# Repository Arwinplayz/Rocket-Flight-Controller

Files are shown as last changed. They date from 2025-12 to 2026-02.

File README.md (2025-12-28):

# Custom Flight Controller
A custom Flight Controller maded within kicad, specificaly for rockets.
---

## Project Overview
The goal was to create a custom Flight Controller which was capable of utilising TVC to guide a rocket.

---

## Screenshots

### 1. Overall
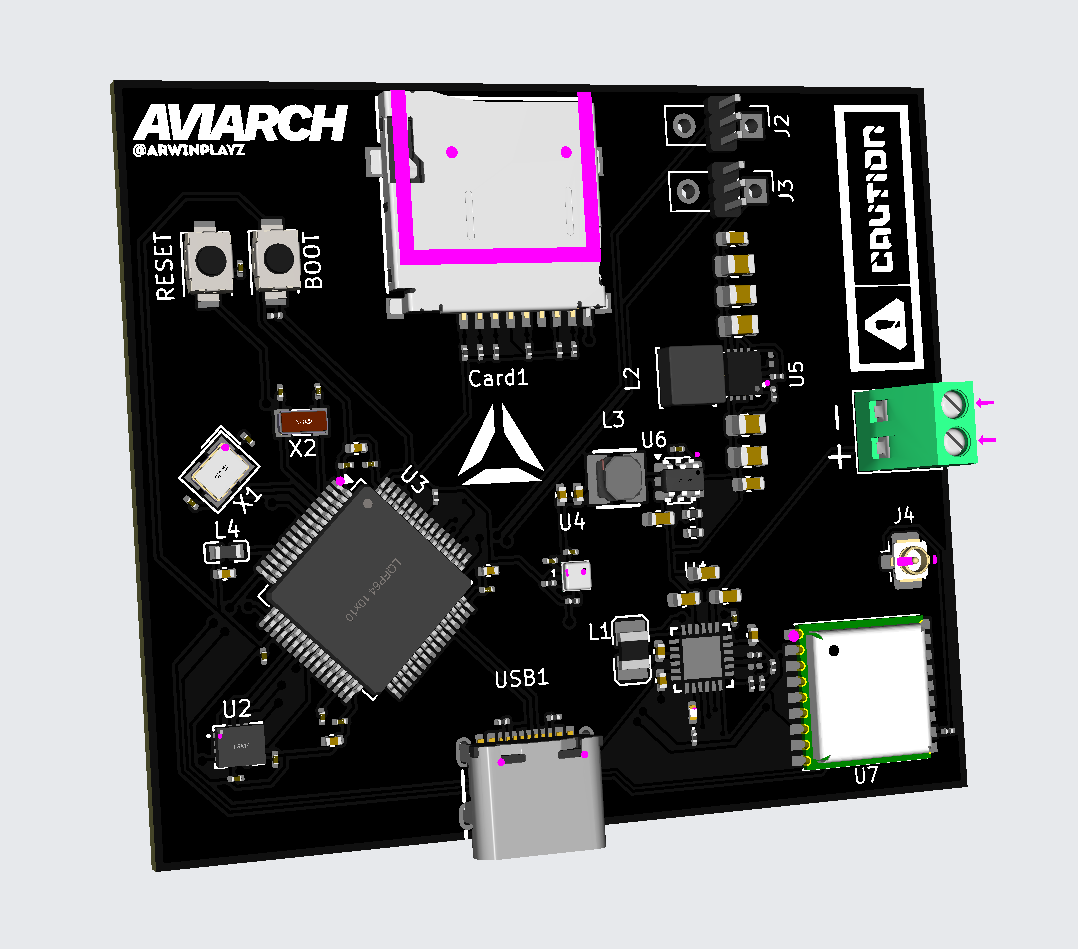
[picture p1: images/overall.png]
Flight Controller Screenshot
  

### 2. Schematic
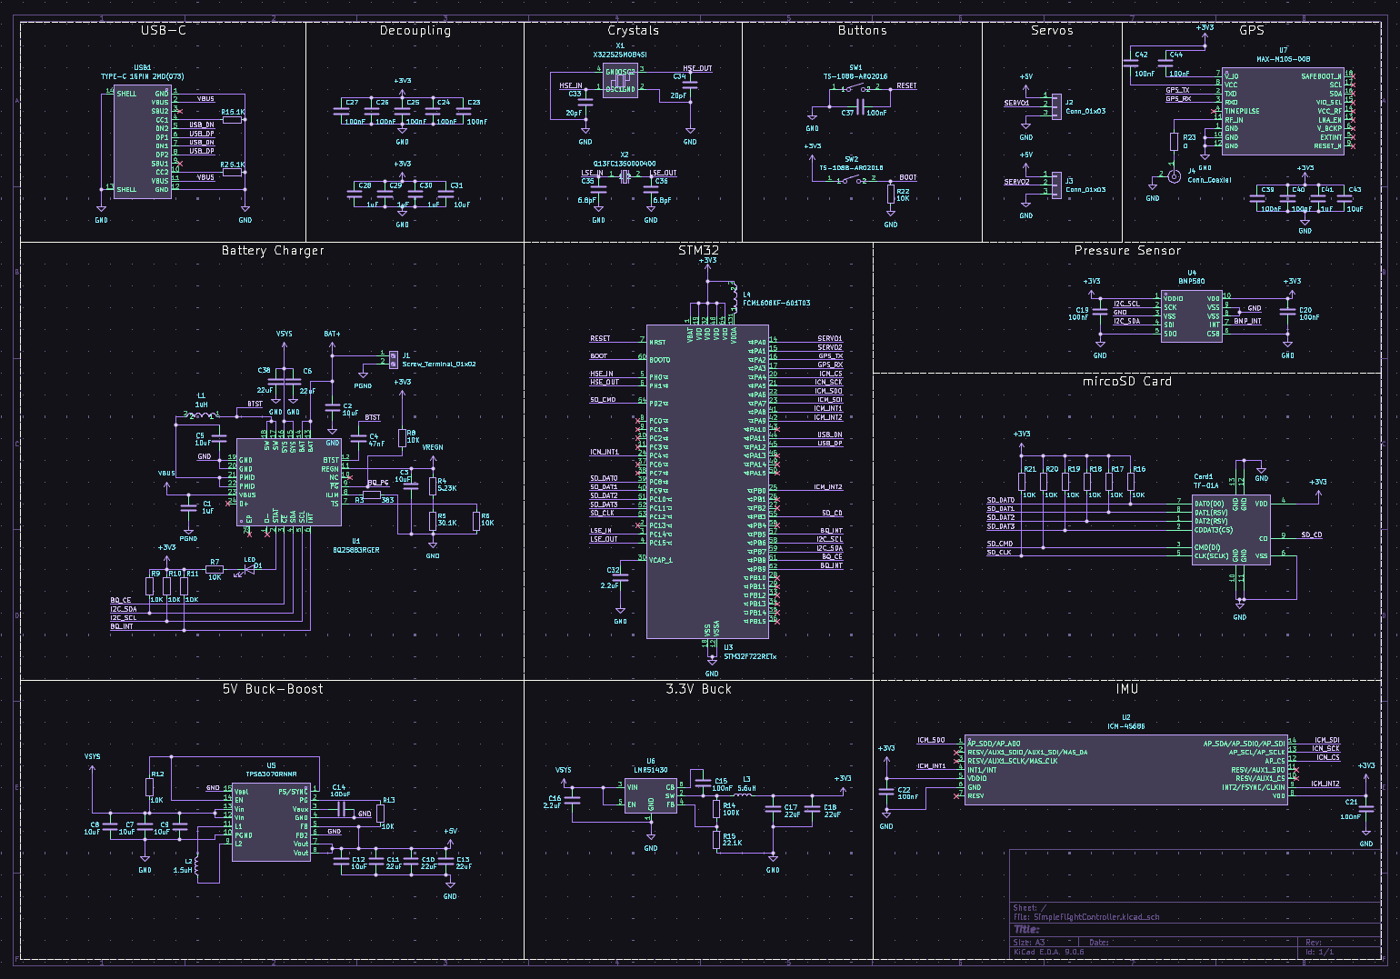
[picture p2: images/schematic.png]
Schematic Screenshot
  

### 3. PCB layout
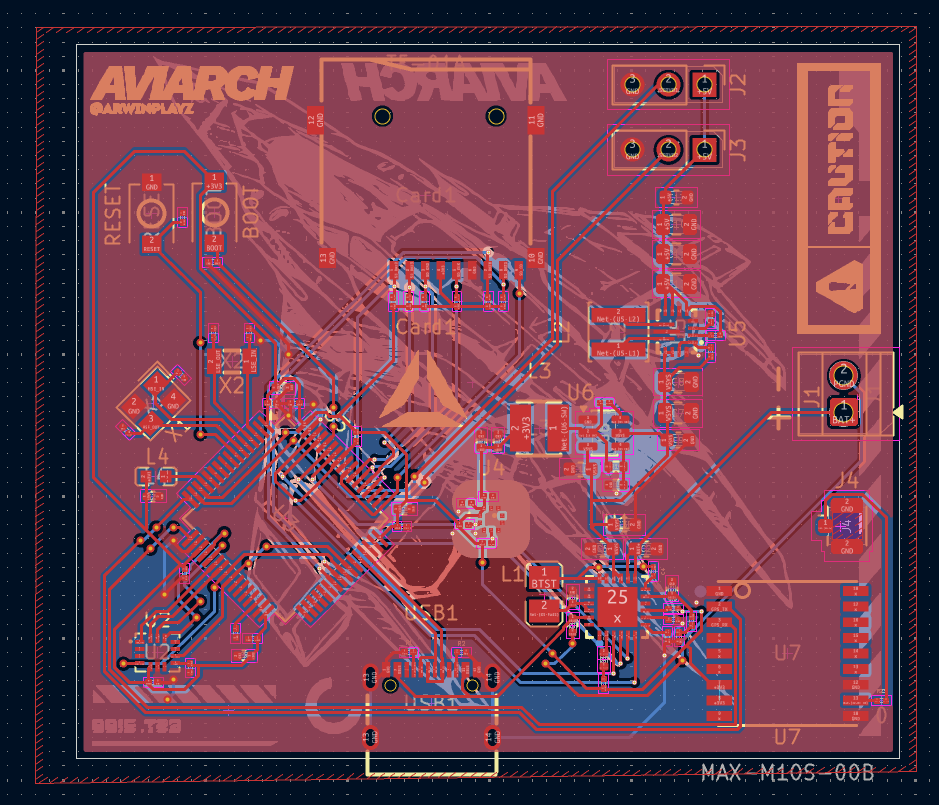
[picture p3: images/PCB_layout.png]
PCB Screenshot
  

### 4. Design
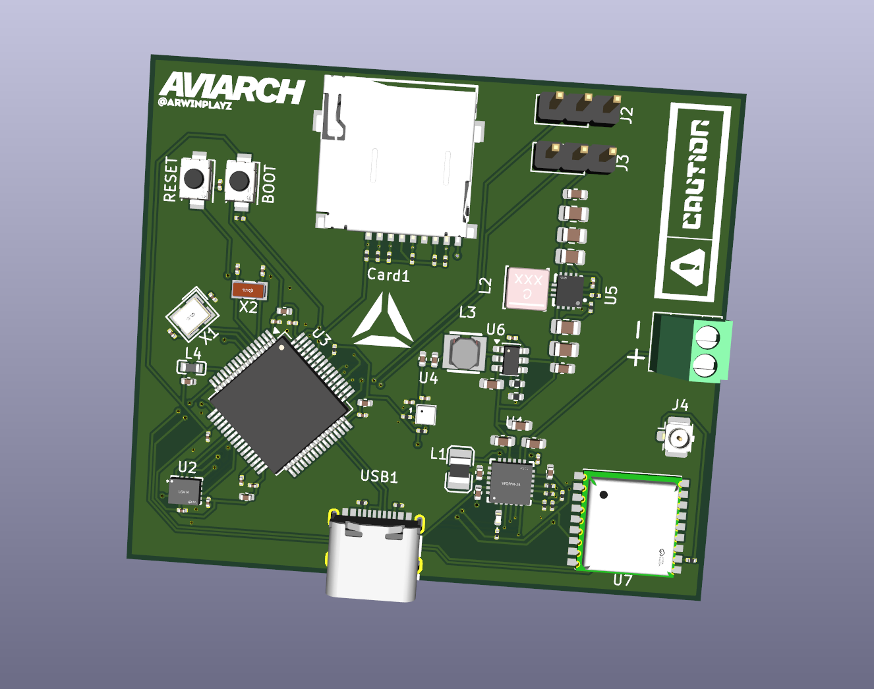
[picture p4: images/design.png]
Design Screenshot


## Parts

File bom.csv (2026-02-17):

Designator | Footprint | Quantity | Value | LCSC Part #
BOOT, RESET | SW-SMD_L3.9-W3.0-P4.45 | 2 | TS-1088-AR02016 | C720477
C1, C28, C29, C30 | 0402 | 4 | 1uF
C10, C11, C13 | 0805 | 3 | 22uF
C12, C2, C9 | 0603 | 3 | 10uF
C14 | 0201 | 1 | 100uF
C15, C19, C20, C21, C22, C23, C24, C25, C26, C27, C37 | 0201 | 11 | 100nF
C16 | 0603 | 1 | 2.2uF
C17, C18 | 0402 | 2 | 22uF
C3, C31, C5 | 0402 | 3 | 10uF
C32 | 0201 | 1 | 2.2uF
C33, C34 | 0201 | 2 | 20pF
C35, C36 | 0201 | 2 | 6.8pF
C38, C6 | 0603 | 2 | 22uF
C4 | 0201 | 1 | 47nF
C7, C8 | 0805 | 2 | 10uF
CARD1 | TF-SMD_TF-01A | 1 | TF-01A | C91145
D1 | 0402 | 1 | LED
J1 | TerminalBlock_Xinya_XY308-2.54-2P_1x02_P2.54mm_Horizontal | 1 | Screw_Terminal_01x02
J2, J3 | PinHeader_1x03_P2.54mm_Vertical | 2 | Conn_01x03
J4 | U.FL_Hirose_U.FL-R-SMT-1_Vertical | 1 | Conn_Coaxial
L1 | L2520 | 1 | 1uH | C435392
L2 | IND-SMD_L4.0-W4.0-A | 1 | 1.5uH
L3 | IND-SMD_L3.0-W3.0 | 1 | 5.6uH
L4 | L0603 | 1 | FCM1608KF-601T03 | C141723
R1, R2 | 0201 | 2 | 5.1K
R10, R11, R12, R13, R16, R17, R18, R19, R20, R21, R22, R6, R7, R8, R9 | 0201 | 15 | 10K
R14 | 0402 | 1 | 100K
R15 | 0402 | 1 | 22.1K
R23 | 0201 | 1 | 0
R3 | 0201 | 1 | 383
R4 | 0201 | 1 | 5.23K
R5 | 0201 | 1 | 30.1K
U1 | VFQFPN-24_L4.0-W4.0-P0.50-BL-EP2.8 | 1 | BQ25883RGER | C544362
U2 | LGA-14_L3.0-W2.5-P0.50-TL | 1 | ICM-45686 | C22459454
U3 | LQFP-64_10x10mm_P0.5mm | 1 | STM32F722RETx
U4 | LGA-10_L2.0-W2.0-P0.50-TL_BMP580 | 1 | BMP580 | C22391138
U5 | VQFN-HR-15_L3.0-W2.5-P0.50-BL_TPS63070RNMR | 1 | TPS63070RNMR | C109322
U6 | SOT-23-6 | 1 | LMR51430
U7 | SMD-18_L10.1-W9.7-P1.10-TL_SKG09F | 1 | MAX-M10S-00B | C4153167
USB1 | USB-C-SMD_TYPE-C-6PIN-2MD-073 | 1 | TYPE-C 16PIN 2MD(073) | C2765186
X1 | CRYSTAL-SMD_4P-L3.2-W2.5-BL | 1 | X322525MOB4SI | C9006
X2 | FC-135R_L3.2-W1.5 | 1 | Q13FC1350000400 | C32346

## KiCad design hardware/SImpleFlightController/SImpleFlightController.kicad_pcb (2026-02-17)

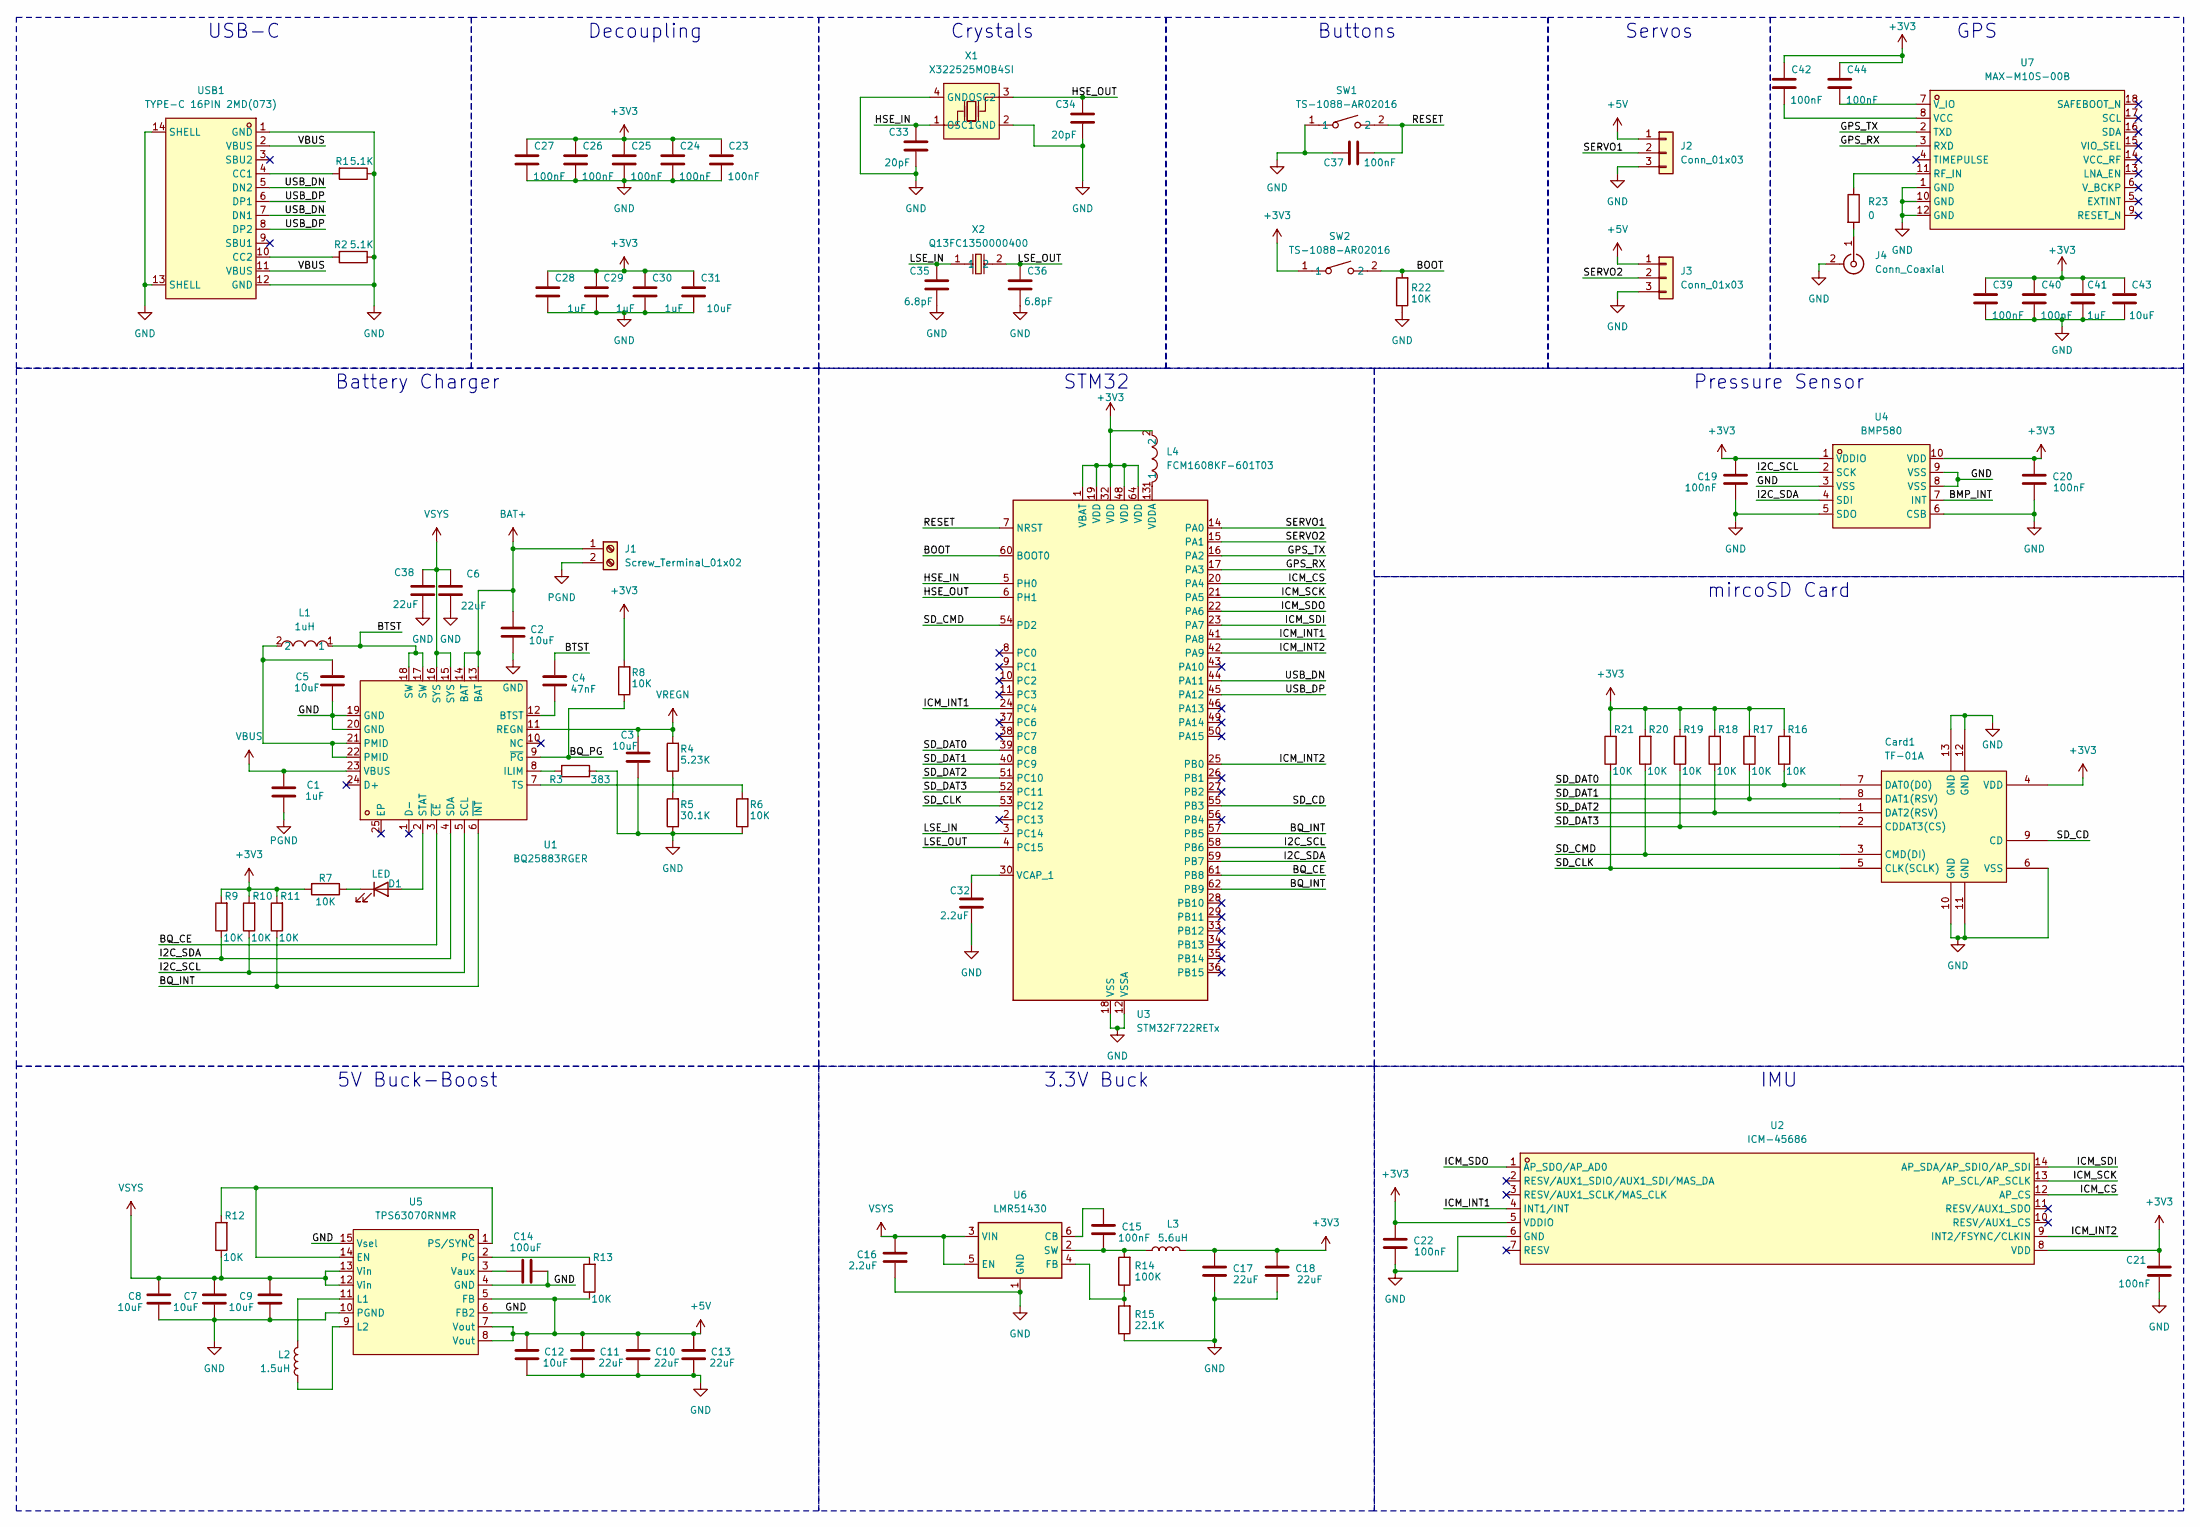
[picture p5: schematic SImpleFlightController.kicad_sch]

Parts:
C1, C28, C29, C30, C41: 1uF; C_0402_1005Metric
C2, C9, C12: 10uF; C_0603_1608Metric
C3, C5, C31, C43: 10uF; C_0402_1005Metric
C4: 47nF; C_0201_0603Metric
C6, C38: 22uF; C_0603_1608Metric
C7, C8: 10uF; C_0805_2012Metric
C10, C11, C13: 22uF; C_0805_2012Metric
C14: 100uF; C_0201_0603Metric
C15, C19, C20, C21, C22, C23, C24, C25, C26, C27, C37: 100nF; C_0201_0603Metric
C16: 2.2uF; C_0603_1608Metric
C17, C18: 22uF; C_0402_1005Metric
C32: 2.2uF; C_0201_0603Metric
C33, C34: 20pF; C_0201_0603Metric
C35, C36: 6.8pF; C_0201_0603Metric
C39, C40, C42, C44: 100nF; C_0402_1005Metric
Card1: TF-01A; TF-SMD_TF-01A; LCSC Part C91145
D1: LED; LED_0402_1005Metric
J1: Screw_Terminal_01x02; TerminalBlock_Xinya_XY308-2.54-2P_1x02_P2.54mm_Horizontal
J2, J3: Conn_01x03; PinHeader_1x03_P2.54mm_Vertical
J4: Conn_Coaxial; U.FL_Hirose_U.FL-R-SMT-1_Vertical
L1: 1uH; L2520; LCSC Part C435392
L2: 1.5uH; IND-SMD_L4.0-W4.0-A
L3: 5.6uH; IND-SMD_L3.0-W3.0
L4: FCM1608KF-601T03; L0603; LCSC Part C141723
R1, R2: 5.1K; R_0201_0603Metric
R3: 383; R_0201_0603Metric
R4: 5.23K; R_0201_0603Metric
R5: 30.1K; R_0201_0603Metric
R6, R7, R8, R9, R10, R11, R12, R13, R16, R17, R18, R19, R20, R21, R22: 10K; R_0201_0603Metric
R14: 100K; R_0402_1005Metric
R15: 22.1K; R_0402_1005Metric
R23: 0; R_0201_0603Metric
SW1, SW2: TS-1088-AR02016; SW-SMD_L3.9-W3.0-P4.45; LCSC Part C720477
U1: BQ25883RGER; VFQFPN-24_L4.0-W4.0-P0.50-BL-EP2.8; LCSC Part C544362
U2: ICM-45686; LGA-14_L3.0-W2.5-P0.50-TL; LCSC Part C22459454
U3: STM32F722RETx; LQFP-64_10x10mm_P0.5mm
U4: BMP580; LGA-10_L2.0-W2.0-P0.50-TL_BMP580; LCSC Part C22391138
U5: TPS63070RNMR; VQFN-HR-15_L3.0-W2.5-P0.50-BL_TPS63070RNMR; LCSC Part C109322
U6: LMR51430; SOT-23-6
U7: MAX-M10S-00B; SMD-18_L10.1-W9.7-P1.10-TL_SKG09F; LCSC Part C4153167
USB1: TYPE-C 16PIN 2MD(073); USB-C-SMD_TYPE-C-6PIN-2MD-073; LCSC Part C2765186
X1: X322525MOB4SI; CRYSTAL-SMD_4P-L3.2-W2.5-BL; LCSC Part C9006
X2: Q13FC1350000400; FC-135R_L3.2-W1.5; LCSC Part C32346

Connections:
+3V3: C17.1, C18.1, C19.1, C20.1, C21.1, C22.1, C23.1, C24.1, C25.1, C26.1, C27.1, C28.1, C29.1, C30.1, C31.1, C39.1, C40.1, C41.1, C42.1, C42.2, C43.1, C44.1, C44.2, Card1.4 (VDD), L3.2, L4.2, R7.2, R8.2, R9.2, R10.2, R11.2, R16.2, R17.2, R18.2, R19.2, R20.2, R21.2, SW2.1, U2.5 (VDDIO), U2.8 (VDD), U3.1 (VBAT), U3.19 (VDD), U3.32 (VDD), U3.48 (VDD), U3.64 (VDD), U4.1 (VDDIO), U4.10 (VDD), U7.7 (V_IO), U7.8 (VCC); also elsewhere on the board
+5V: C10.1, C11.1, C12.1, C13.1, J2.1, J3.1, R13.1, U5.5 (FB), U5.7 (Vout), U5.8 (Vout)
/BMP_INT: U4.7 (INT)
/BOOT: R22.2, SW2.2, U3.60 (BOOT0); also elsewhere on the board
/BQ_CE: U1.3 (~CE), U3.61 (PB8)
/BQ_INT: R11.1, U1.6 (~INT), U3.57 (PB5), U3.62 (PB9)
/BQ_PG: R8.1, U1.9 (~PG)
/BTST: C4.1, L1.1, U1.17 (SW), U1.18 (SW)
/GPS_RX: U3.17 (PA3), U7.3 (RXD)
/GPS_TX: U3.16 (PA2), U7.2 (TXD)
/HSE_IN: C33.1, U3.5 (PH0), X1.1 (OSC1)
/HSE_OUT: C34.1, U3.6 (PH1), X1.3 (OSC2)
/I2C_SCL: R10.1, U1.5 (SCL), U3.58 (PB6), U4.2 (SCK)
/I2C_SDA: R9.1, U1.4 (SDA), U3.59 (PB7), U4.4 (SDI)
/ICM_CS: U2.12 (AP_CS), U3.20 (PA4)
/ICM_INT1: U2.4 (INT1/INT), U3.24 (PC4), U3.41 (PA8)
/ICM_INT2: U2.9 (INT2/FSYNC/CLKIN), U3.25 (PB0), U3.42 (PA9)
/ICM_SCK: U2.13 (AP_SCL/AP_SCLK), U3.21 (PA5)
/ICM_SDI: U2.14 (AP_SDA/AP_SDIO/AP_SDI), U3.23 (PA7)
/ICM_SDO: U2.1 (AP_SDO/AP_AD0), U3.22 (PA6)
/LSE_IN: C35.1, U3.3 (PC14), X2.1
/LSE_OUT: C36.1, U3.4 (PC15), X2.2
/RESET: C37.2, SW1.2, U3.7 (NRST); also elsewhere on the board
/SD_CD: Card1.9 (CD), U3.55 (PB3)
/SD_CLK: Card1.5 (CLK(SCLK)), R21.1, U3.53 (PC12)
/SD_CMD: Card1.3 (CMD(DI)), R20.1, U3.54 (PD2)
/SD_DAT0: Card1.7 (DAT0(D0)), R16.1, U3.39 (PC8)
/SD_DAT1: Card1.8 (DAT1(RSV)), R17.1, U3.40 (PC9)
/SD_DAT2: Card1.1 (DAT2(RSV)), R18.1, U3.51 (PC10)
/SD_DAT3: Card1.2 (CDDAT3(CS)), R19.1, U3.52 (PC11)
/SERVO1: J2.2, U3.14 (PA0)
/SERVO2: J3.2, U3.15 (PA1)
/USB_DN: U3.44 (PA11), USB1.5 (DN2), USB1.7 (DN1)
/USB_DP: U3.45 (PA12), USB1.6 (DP1), USB1.8 (DP2)
BAT+: C2.1, J1.1, U1.13 (BAT), U1.14 (BAT)
GND: C2.2, C3.2, C5.2, C6.2, C7.2, C8.2, C9.2, C10.2, C11.2, C12.2, C13.2, C14.1, C16.2, C17.2, C18.2, C19.2, C20.2, C21.2, C22.2, C23.2, C24.2, C25.2, C26.2, C27.2, C28.2, C29.2, C30.2, C31.2, C32.2, C33.2, C34.2, C35.2, C36.2, C37.1, C38.2, C39.2, C40.2, C41.2, C43.2, Card1.6 (VSS), Card1.10 (GND), Card1.11 (GND), Card1.12 (GND), Card1.13 (GND), J2.3, J3.3, J4.2 (Ext), R1.1, R2.1, R3.1, R5.1, R6.1, R15.1, R22.1, SW1.1, U1.19 (GND), U1.20 (GND), U2.6 (GND), U3.12 (VSSA), U3.18 (VSS), U3.31 (VSS), U3.47 (VSS), U3.63 (VSS), U4.3 (VSS), U4.5 (SDO), U4.6 (CSB), U4.8 (VSS), U4.9 (VSS), U5.4 (GND), U5.6 (FB2), U5.10 (PGND), U5.15 (Vsel), U6.1 (GND), U7.1 (GND), U7.10 (GND), U7.12 (GND), USB1.1 (GND), USB1.12 (GND), USB1.13 (SHELL), USB1.14 (SHELL), X1.2 (GND), X1.4 (GND); also elsewhere on the board
unnamed: C5.1, L1.2, U1.21 (PMID), U1.22 (PMID)
unnamed: D1.2 (A), U1.2 (STAT)
unnamed: D1.1 (K), R7.1
unnamed: J4.1 (In), R23.2
unnamed: R4.1, R5.2
unnamed: C4.2, U1.12 (BTST)
unnamed: R3.2, U1.8 (ILIM)
unnamed: R6.2, U1.7 (TS)
unnamed: C32.1, U3.30 (VCAP_1)
unnamed: L4.1, U3.13 (VDDA)
unnamed: R12.2, U5.1 (PS/SYNC), U5.14 (EN)
unnamed: L2.1, U5.11 (L1)
unnamed: L2.2, U5.9 (L2)
unnamed: R13.2, U5.2 (PG)
unnamed: C14.2, U5.3 (Vaux)
unnamed: C15.1, U6.6 (CB)
unnamed: R14.1, R15.2, U6.4 (FB)
unnamed: C15.2, L3.1, R14.2, U6.2 (SW)
unnamed: R23.1, U7.11 (RF_IN)
unnamed: R1.2, USB1.4 (CC1)
unnamed: R2.2, USB1.10 (CC2)
PGND: C1.2, J1.2
VBUS: C1.1, U1.23 (VBUS), USB1.2 (VBUS), USB1.11 (VBUS)
VREGN: C3.1, R4.2, U1.11 (REGN)
VSYS: C6.1, C7.1, C8.1, C9.1, C16.1, C38.1, R12.1, U1.15 (SYS), U1.16 (SYS), U5.12 (Vin), U5.13 (Vin), U6.3 (VIN), U6.5 (EN)

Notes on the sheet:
Buttons
mircoSD Card
USB-C
Crystals
GPS
Servos
Battery Charger
STM32
IMU
5V Buck-Boost
Pressure Sensor
Decoupling
3.3V Buck

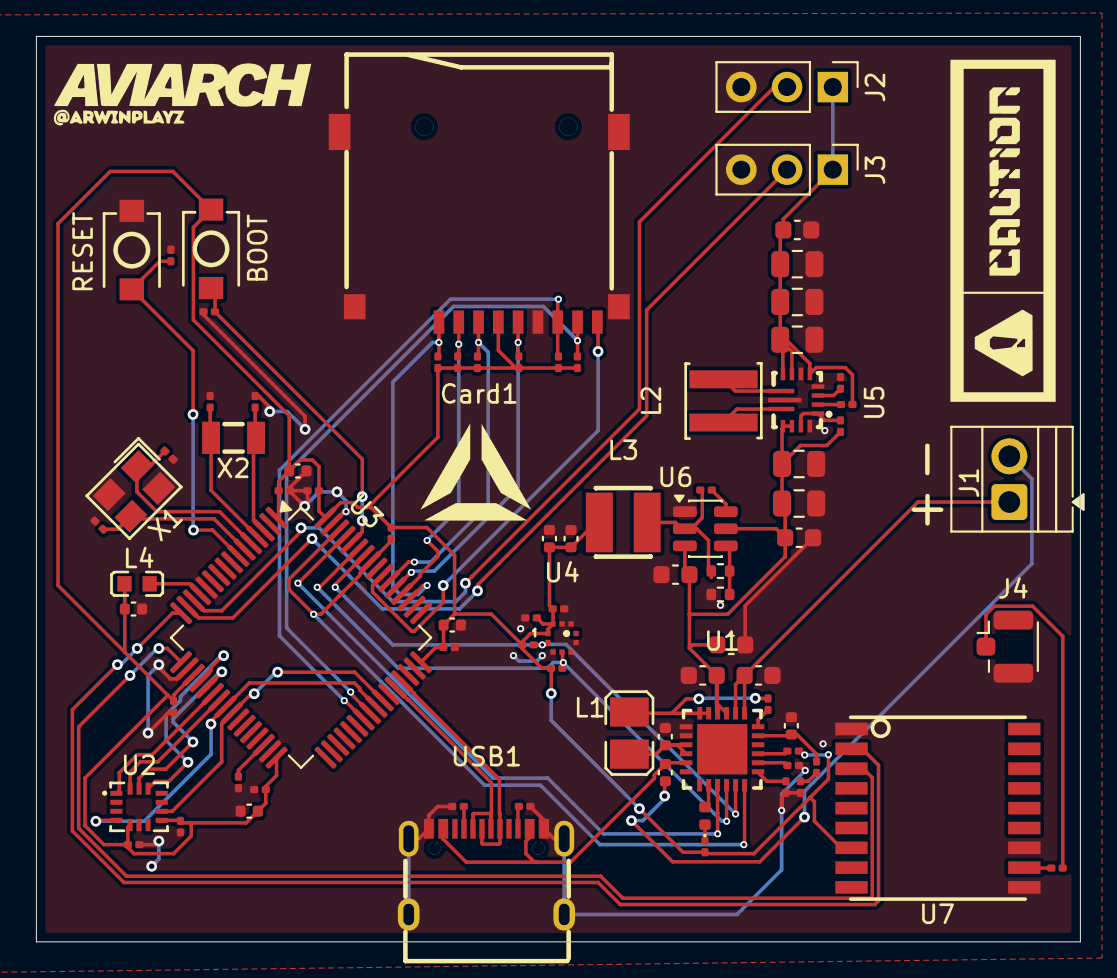
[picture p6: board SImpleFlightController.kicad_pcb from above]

Board: 2 copper layers, 58.0 x 50.3 mm, 83 parts (0 on the bottom side), 60 nets.

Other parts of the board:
BOOT: TS-1088-AR02016; SW-SMD_L3.9-W3.0-P4.45
RESET: TS-1088-AR02016; SW-SMD_L3.9-W3.0-P4.45

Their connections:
+3V3: BOOT.1; also elsewhere on the board
/BOOT: BOOT.2; also elsewhere on the board
/RESET: RESET.2; also elsewhere on the board
GND: RESET.1; also elsewhere on the board

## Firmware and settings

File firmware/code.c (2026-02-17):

#include "stm32f7xx_hal.h"
#include <math.h>

I2C_HandleTypeDef hi2c1;
TIM_HandleTypeDef htim3;

#define IMU_I2C_ADDR (0x68 << 1)
#define IMU_REG_WHO_AM_I 0x75
#define IMU_REG_PWR_MGMT 0x06
#define IMU_REG_ACCEL_XOUT_H 0x2D
#define IMU_REG_GYRO_XOUT_H 0x33

#define SERVO_TIMER htim3
#define SERVO_CHANNEL TIM_CHANNEL_1
#define SERVO_PWM_FREQ_HZ 50.0f
#define SERVO_MIN_PULSE_US 1000.0f
#define SERVO_MAX_PULSE_US 2000.0f

#define LOOP_DT_S 0.002f
#define COMPLEMENTARY_ALPHA 0.98f

void SystemClock_Config(void);
static void MX_GPIO_Init(void);
static void MX_I2C1_Init(void);
static void MX_TIM3_Init(void);

static void IMU_Init(void);
static void IMU_ReadRaw(int16_t *ax, int16_t *az, int16_t *gx);
static float map_pitch_to_pulse(float pitch_deg);

int main(void)
{
    HAL_Init();
    SystemClock_Config();
    MX_GPIO_Init();
    MX_I2C1_Init();
    MX_TIM3_Init();
    IMU_Init();
    HAL_TIM_PWM_Start(&SERVO_TIMER, SERVO_CHANNEL);

    float pitch_deg = 0.0f;

    while (1)
    {
        static uint32_t last_tick = 0;
        uint32_t now = HAL_GetTick();
        if (now - last_tick < (uint32_t)(LOOP_DT_S * 1000.0f)) continue;
        last_tick = now;

        int16_t ax_raw, az_raw, gx_raw;
        IMU_ReadRaw(&ax_raw, &az_raw, &gx_raw);

        float ax = (float)ax_raw / 16384.0f;
        float az = (float)az_raw / 16384.0f;
        float gx = (float)gx_raw / 131.0f;

        float pitch_acc = atan2f(-ax, az) * 180.0f / (float)M_PI;
        float pitch_gyro = pitch_deg + gx * LOOP_DT_S;
        pitch_deg = COMPLEMENTARY_ALPHA * pitch_gyro + (1.0f - COMPLEMENTARY_ALPHA) * pitch_acc;

        float pulse_us = map_pitch_to_pulse(pitch_deg);

        uint32_t timer_clk = HAL_RCC_GetPCLK1Freq() * 2;
        float timer_freq = 1000000.0f;
        uint32_t period = (uint32_t)(timer_freq / SERVO_PWM_FREQ_HZ) - 1;
        uint32_t compare = (uint32_t)((pulse_us / 1000000.0f) * timer_freq);

        __HAL_TIM_SET_AUTORELOAD(&SERVO_TIMER, period);
        __HAL_TIM_SET_COMPARE(&SERVO_TIMER, SERVO_CHANNEL, compare);
    }
}

static void IMU_WriteReg(uint8_t reg, uint8_t val)
{
    HAL_I2C_Mem_Write(&hi2c1, IMU_I2C_ADDR, reg, I2C_MEMADD_SIZE_8BIT, &val, 1, 100);
}

static void IMU_ReadRegs(uint8_t reg, uint8_t *buf, uint16_t len)
{
    HAL_I2C_Mem_Read(&hi2c1, IMU_I2C_ADDR, reg, I2C_MEMADD_SIZE_8BIT, buf, len, 100);
}

static void IMU_Init(void)
{
    HAL_Delay(100);
    IMU_WriteReg(IMU_REG_PWR_MGMT, 0x00);
    HAL_Delay(10);
}

static void IMU_ReadRaw(int16_t *ax, int16_t *az, int16_t *gx)
{
    uint8_t buf[12];
    IMU_ReadRegs(IMU_REG_ACCEL_XOUT_H, buf, 12);

    *ax = (int16_t)((buf[0] << 8) | buf[1]);
    *az = (int16_t)((buf[4] << 8) | buf[5]);
    *gx = (int16_t)((buf[8] << 8) | buf[9]);
}

static float map_pitch_to_pulse(float pitch_deg)
{
    if (pitch_deg < -45.0f) pitch_deg = -45.0f;
    if (pitch_deg > 45.0f) pitch_deg = 45.0f;
    float t = (pitch_deg + 45.0f) / 90.0f;
    return SERVO_MIN_PULSE_US + t * (SERVO_MAX_PULSE_US - SERVO_MIN_PULSE_US);
}

void SystemClock_Config(void)
{
    RCC_OscInitTypeDef RCC_OscInitStruct = {0};
    RCC_ClkInitTypeDef RCC_ClkInitStruct = {0};

    __HAL_RCC_PWR_CLK_ENABLE();
    __HAL_PWR_VOLTAGESCALING_CONFIG(PWR_REGULATOR_VOLTAGE_SCALE1);

    RCC_OscInitStruct.OscillatorType = RCC_OSCILLATORTYPE_HSE;
    RCC_OscInitStruct.HSEState = RCC_HSE_ON;
    RCC_OscInitStruct.PLL.PLLState = RCC_PLL_ON;
    RCC_OscInitStruct.PLL.PLLSource = RCC_PLLSOURCE_HSE;
    RCC_OscInitStruct.PLL.PLLM = 8;
    RCC_OscInitStruct.PLL.PLLN = 216;
    RCC_OscInitStruct.PLL.PLLP = RCC_PLLP_DIV2;
    RCC_OscInitStruct.PLL.PLLQ = 9;
    HAL_RCC_OscConfig(&RCC_OscInitStruct);

    HAL_PWREx_EnableOverDrive();

    RCC_ClkInitStruct.ClockType = RCC_CLOCKTYPE_HCLK | RCC_CLOCKTYPE_SYSCLK |
                                  RCC_CLOCKTYPE_PCLK1 | RCC_CLOCKTYPE_PCLK2;
    RCC_ClkInitStruct.SYSCLKSource = RCC_SYSCLKSOURCE_PLLCLK;
    RCC_ClkInitStruct.AHBCLKDivider = RCC_SYSCLK_DIV1;
    RCC_ClkInitStruct.APB1CLKDivider = RCC_HCLK_DIV4;
    RCC_ClkInitStruct.APB2CLKDivider = RCC_HCLK_DIV2;
    HAL_RCC_ClockConfig(&RCC_ClkInitStruct, FLASH_LATENCY_7);
}

static void MX_I2C1_Init(void)
{
    __HAL_RCC_I2C1_CLK_ENABLE();

    hi2c1.Instance = I2C1;
    hi2c1.Init.Timing = 0x20404768;
    hi2c1.Init.OwnAddress1 = 0;
    hi2c1.Init.AddressingMode = I2C_ADDRESSINGMODE_7BIT;
    hi2c1.Init.DualAddressMode = I2C_DUALADDRESS_DISABLE;
    hi2c1.Init.OwnAddress2 = 0;
    hi2c1.Init.OwnAddress2Masks = I2C_OA2_NOMASK;
    hi2c1.Init.GeneralCallMode = I2C_GENERALCALL_DISABLE;
    hi2c1.Init.NoStretchMode = I2C_NOSTRETCH_DISABLE;
    HAL_I2C_Init(&hi2c1);
    HAL_I2CEx_ConfigAnalogFilter(&hi2c1, I2C_ANALOGFILTER_ENABLE);
}

static void MX_TIM3_Init(void)
{
    __HAL_RCC_TIM3_CLK_ENABLE();

    uint32_t timer_clk = HAL_RCC_GetPCLK1Freq() * 2;
    uint32_t prescaler = (timer_clk / 1000000U) - 1U;

    htim3.Instance = TIM3;
    htim3.Init.Prescaler = prescaler;
    htim3.Init.CounterMode = TIM_COUNTERMODE_UP;
    htim3.Init.Period = 20000 - 1;
    htim3.Init.ClockDivision = TIM_CLOCKDIVISION_DIV1;
    htim3.Init.AutoReloadPreload = TIM_AUTORELOAD_PRELOAD_DISABLE;
    HAL_TIM_PWM_Init(&htim3);

    TIM_OC_InitTypeDef sConfigOC = {0};
    sConfigOC.OCMode = TIM_OCMODE_PWM1;
    sConfigOC.Pulse = 1500;
    sConfigOC.OCPolarity = TIM_OCPOLARITY_HIGH;
    sConfigOC.OCFastMode = TIM_OCFAST_DISABLE;
    HAL_TIM_PWM_ConfigChannel(&htim3, &sConfigOC, SERVO_CHANNEL);
}

static void MX_GPIO_Init(void)
{
    __HAL_RCC_GPIOA_CLK_ENABLE();
    __HAL_RCC_GPIOB_CLK_ENABLE();

    GPIO_InitTypeDef GPIO_InitStruct = {0};

    GPIO_InitStruct.Pin = GPIO_PIN_8 | GPIO_PIN_9;
    GPIO_InitStruct.Mode = GPIO_MODE_AF_OD;
    GPIO_InitStruct.Pull = GPIO_PULLUP;
    GPIO_InitStruct.Speed = GPIO_SPEED_FREQ_VERY_HIGH;
    GPIO_InitStruct.Alternate = GPIO_AF4_I2C1;
    HAL_GPIO_Init(GPIOB, &GPIO_InitStruct);

    GPIO_InitStruct.Pin = GPIO_PIN_6;
    GPIO_InitStruct.Mode = GPIO_MODE_AF_PP;
    GPIO_InitStruct.Pull = GPIO_NOPULL;
    GPIO_InitStruct.Speed = GPIO_SPEED_FREQ_LOW;
    GPIO_InitStruct.Alternate = GPIO_AF2_TIM3;
    HAL_GPIO_Init(GPIOA, &GPIO_InitStruct);
}

void Error_Handler(void)
{
    __disable_irq();
    while (1) {}
}

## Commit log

2025-12-20 added local files
    [SImpleFlightController.kicad_pcb, SImpleFlightController.kicad_sch]
2025-12-24 updated schematics
    [SImpleFlightController.kicad_pcb, SImpleFlightController.kicad_sch]
2026-02-17 updated GPS to front
    [SImpleFlightController.kicad_pcb, SImpleFlightController.kicad_sch, bom.csv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]
